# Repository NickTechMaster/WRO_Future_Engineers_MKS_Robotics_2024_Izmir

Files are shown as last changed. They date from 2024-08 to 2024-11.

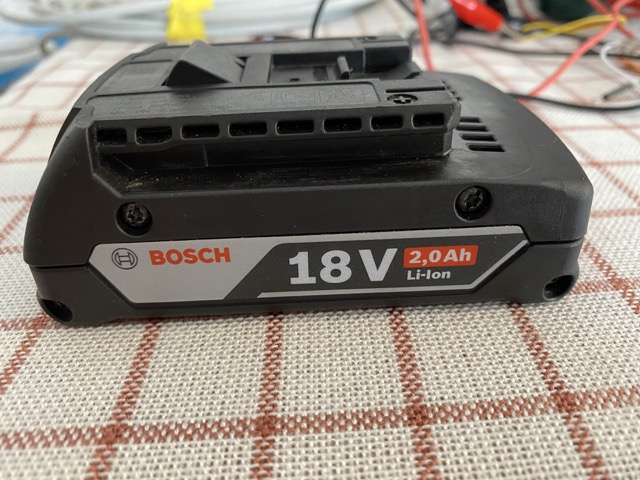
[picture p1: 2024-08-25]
2. Energy & Sensors/battery_1.jpeg

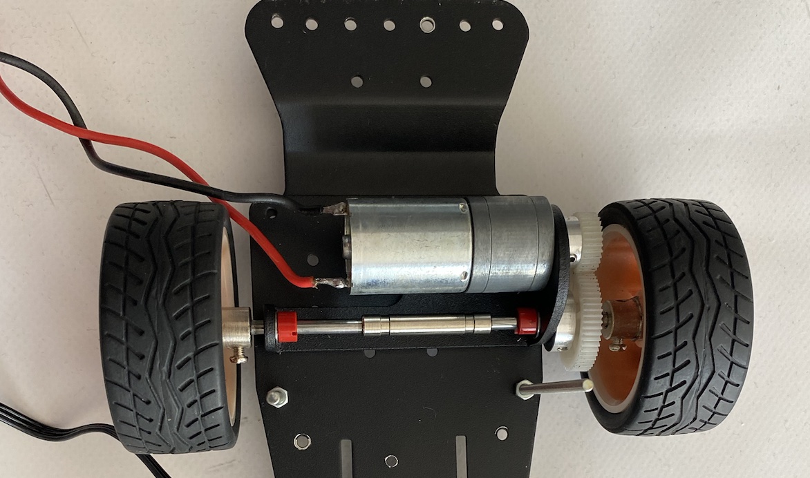
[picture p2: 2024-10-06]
1. Motorization/engine_1.jpg

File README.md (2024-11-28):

banner_Mks_Robotics-DownScaled

<h3>Infos of the GitHub Structure</h3>

Our GitHub documentation is structured according to the evaluation criteria of the WRO Future Engineers category. Under points 1-5, you will find information and materials that correspond to the evaluation criteria. Below that, under points a-f, we provide additional important information from our perspective.<br><hr>

<h3>Table of contents</h3>

[1. Motorization](https://github.com/NickTechMaster/WRO_Future_Engineers_MKS_Robotics_2024_Izmir/tree/main/1.%20Motorization
)<br>

[2. Energy & Sensors](https://github.com/NickTechMaster/WRO_Future_Engineers_MKS_Robotics_2024_Izmir/tree/main/2.%20Energy%20%26%20Sensors
)<br> 

[3. Obstacle Race](https://github.com/NickTechMaster/WRO_Future_Engineers_MKS_Robotics_2024_Izmir/tree/main/3.%20Obstacle%20Race%20
)<br>

[4. Photos](https://github.com/NickTechMaster/WRO_Future_Engineers_MKS_Robotics_2024_Izmir/tree/main/4.%20Photos
)<br>

[5. Videos](https://github.com/NickTechMaster/WRO_Future_Engineers_MKS_Robotics_2024_Izmir/tree/main/5.%20Videos
)<br>

[a. 3d printing](https://github.com/NickTechMaster/WRO_Future_Engineers_MKS_Robotics_2024_Izmir/tree/main/a.%203d%20printing
)<br>

[b. diagrams](https://github.com/NickTechMaster/WRO_Future_Engineers_MKS_Robotics_2024_Izmir/tree/main/b.%20diagrams
)<br>

[d. Code](https://github.com/NickTechMaster/WRO_Future_Engineers_MKS_Robotics_2024_Izmir/tree/main/d.%20Code
)<br>

[e. construction manual](https://github.com/NickTechMaster/WRO_Future_Engineers_MKS_Robotics_2024_Izmir/tree/main/e.%20construction%20manual
)<br>

[f. other](https://github.com/NickTechMaster/WRO_Future_Engineers_MKS_Robotics_2024_Izmir/tree/main/f.%20other
)<br>
<hr>

<h3>Introduction</h3>

We are Nico and Julian from Saarland, Germany, and this year we’re proud to once again compete as a team from Maximilian-Kolbe-Schule Wiebelskirchen, a secondary school, in the WRO (World Robot Olympiad) Future Engineers category. Robotics and engineering have been a big part of our lives for several years now, and our interest in this field has grown through numerous school-based projects and competitions.
Our WRO journey began back in 2019 when we participated in the "Mission" category. Though we didn’t qualify for the Germany Finals in our first two attempts, these experiences motivated us to improve and eventually try a new challenge: the "Future Engineers" category. Since making that switch, we’ve reached the national finals multiple times, and this year we reached a major milestone by winning second place at the Germany Finals, which qualified us for the World Finals.

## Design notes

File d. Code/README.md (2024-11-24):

**In this folder, you will find the programming for the robotic car.**

We are using two different Raspberry Pis, so we have a total of four scripts: two for the opening race and two for the obstacle race.

- **drive = driving Raspberry Pi**
- **cam = camera Raspberry Pi**

### Programming for the Opening Race

In this year's opening race, we are using the basic idea from last year. While driving, the robot continuously measures the values from the ultrasonic sensors located at the front, left, and right. Based on the values from the left and right sensors, the robot calculates the center point and steers the autonomous car proportionally to return it to the middle as efficiently as possible. This means that the further the car is from the center, the stronger it steers to get back to it.

For example: If the left ultrasonic sensor reads 10 and the right ultrasonic sensor reads 50, the left sensor is showing a very short distance, meaning the car is quite far to the left near the barrier. If we take the sum of both values, we get 60. Half of that is 30. When both sensors read 30, we know that the robot is exactly in the center. To reach this center, we calculate the percentage difference and steer accordingly.

Since this process is repeated very quickly and frequently, the car may sometimes sway slightly, but this is corrected by the system. To ensure the car stops perfectly after 3 laps, it increases a variable each time it takes a turn. We detect a turn when the color sensor detects orange or blue. The upper Raspberry Pi, which receives this data, sends it to the driving Raspberry Pi. The driving Raspberry Pi counts 12 turns and then continues until the front ultrasonic sensor detects a certain distance, at which point the car stops.

### Programming for the Obstacle Race

For the obstacle race, we use the programming from the opening race as the foundation, since we also need to drive autonomously here. Only when the camera detects a colored block does the upper Raspberry Pi send a signal to the driving Raspberry Pi, which then performs a corresponding evasive maneuver. We go around red blocks to the right and around green blocks to the left. Additionally, we detect turns using the color sensor, where we perform a realignment maneuver.

For color detection of the blocks, we use filters/masks to only see the relevant colors and filter out other potential errors the camera might detect. We then detect the contours of the objects. To adjust the color values of the masks, we wrote an additional script with sliders.

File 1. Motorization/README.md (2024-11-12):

**Motorization**

We used a Funduino kit as the foundation, specifically designed for Future Engineers. However, from this kit, we only used the base plates, distance sleeves, and the steering mechanism. The exact dimensions and measurements of the plates, screws, and other components can be found in the assembly instructions (e. Assembly Instructions).

**Steering**  
For steering, we use a 20-kg servo steering motor. This motor is mounted horizontally on our base plate. A small rod, secured with screws, runs from the servo’s thread to the actual steering axle. This axle connects the two front wheels. When the servo turns in one direction, the entire steering axle shifts, which in turn moves the wheels.

**Drive Motor**  
As the drive motor, we use a standard DC motor, which is operated via the motor controller "L298N." It is directly connected to the 18V battery. The motor is then powered by the motor driver. Three wires extend from the motor controller, which we use to control the motor, and they are connected directly to the controlling Raspberry Pi. The Pi sends a PWM signal. A PWM signal (Pulse Width Modulation) is an electrical signal that varies the "On" and "Off" duration to control power. To drive both wheels simultaneously, we use a gear transmission that transfers the motor’s rotations to a gear firmly attached to the drive axle. The drive axle is split in the middle, but the two ends are connected with a coupling sleeve. This allows one wheel to rotate freely. Previously, we encountered a problem where the car’s wheels would lock due to power issues. Now, with one wheel able to rotate freely, this issue occurs less frequently.

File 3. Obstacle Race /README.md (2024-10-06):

**Obstacle Race Programming**

In the obstacle race, we use a similar programming approach to the one from the opening race for the driving fundamentals, as we also aim to keep the car centered in the middle of the track as much as possible. To achieve this, the Raspberry Pi calculates an average position where the car would be in the middle. It then determines how far the car is from this center in terms of percentage. This percentage is then converted and passed on to the servo motor. Only when the camera detects a colored block, the Raspberry Pi connected to the camera sends a signal to the driving Raspberry Pi. The driving Raspberry Pi then executes a corresponding evasive maneuver. The signals are transmitted using on/off electrical signals. For example, the Raspberry Pi connected to the camera applies a 3-volt current to one of the wires between the two Raspberry Pis. The Raspberry Pis have built-in GPIO pins that send a HIGH signal to communicate. The driving Raspberry Pi checks if there is a current on one of the wires. Depending on which wire is affected, it performs different actions. For red blocks, it steers to the right, and for green blocks, it steers to the left. To detect the color of the blocks, we use filters/masks to isolate specific colors and filter out errors that the camera might detect. We then identify the contours. To set the color values of the masks, we wrote a separate program with sliders. Additionally, the car has several safety maneuvers that are triggered if the front ultrasonic sensors detect that the car is about to hit one of the blocks or the barrier. In such cases, the car reverses.

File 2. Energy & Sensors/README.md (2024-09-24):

**Energy**  
Our car is powered by a standard 18V Bosch battery. This battery is inserted into a battery holder, from which a connection leads to the voltage converter. The converter steps the voltage down to 5V, which we need for the Raspberry Pis, the servo motor, and the ultrasonic sensors. Additionally, a motor controller is used, which is powered directly by 18V. It's important to note that the ultrasonic sensors run on 5V, while other sensors, like the color sensor, operate on 3.3V. The color sensor communicates with the Raspberry Pis via an I²C signal. I²C (Inter-Integrated Circuit) is a serial communication bus that connects devices using two lines.

**Sensors**  
A variety of sensors are installed in our car. First, we have integrated three HCSR-04 ultrasonic sensors, which are used to detect the road and calculate steering. The Raspberry Pi sends GPIO signals to the ultrasonic sensors, waits for the return of the ultrasonic signal, and measures the time between the outgoing and incoming signals to calculate the distance. GPIO (General Purpose Input/Output) signals are digital input and output signals that can be generated or read by a microcontroller, like the Raspberry Pi, to control or communicate with external electronic components. Additionally, we have installed a color sensor that detects orange lines to count laps, allowing us to stop successfully after three laps. At the top, there is also a camera, a USB webcam from Logitech (Brio 500), which is used for obstacle detection. We selected this camera because of its wide-angle lens, exposure adjustment, and color rendering.

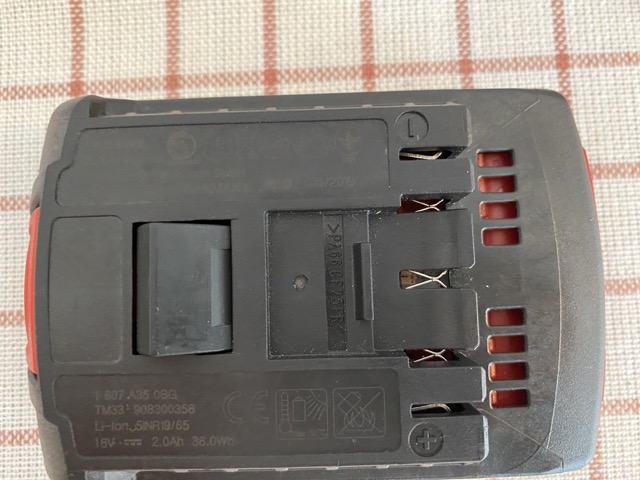
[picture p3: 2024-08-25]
2. Energy & Sensors/battery_2.jpeg

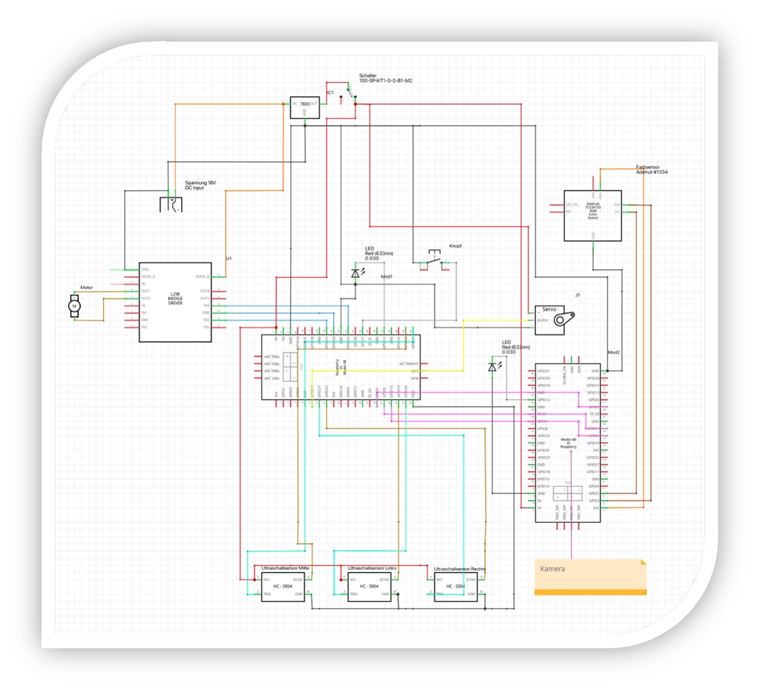
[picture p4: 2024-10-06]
2. Energy & Sensors/circuit_diagram_2.jpg

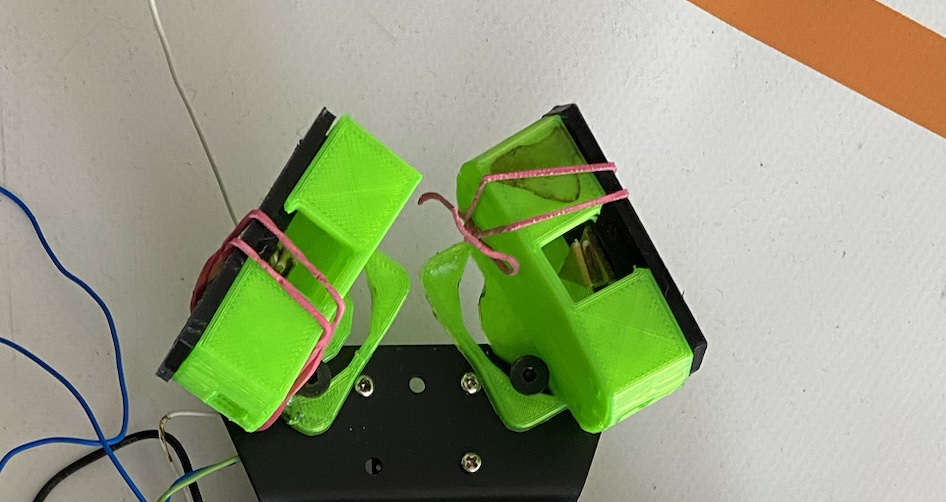
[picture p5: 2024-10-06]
2. Energy & Sensors/ultrasonic_sensor_holder_1.jpg

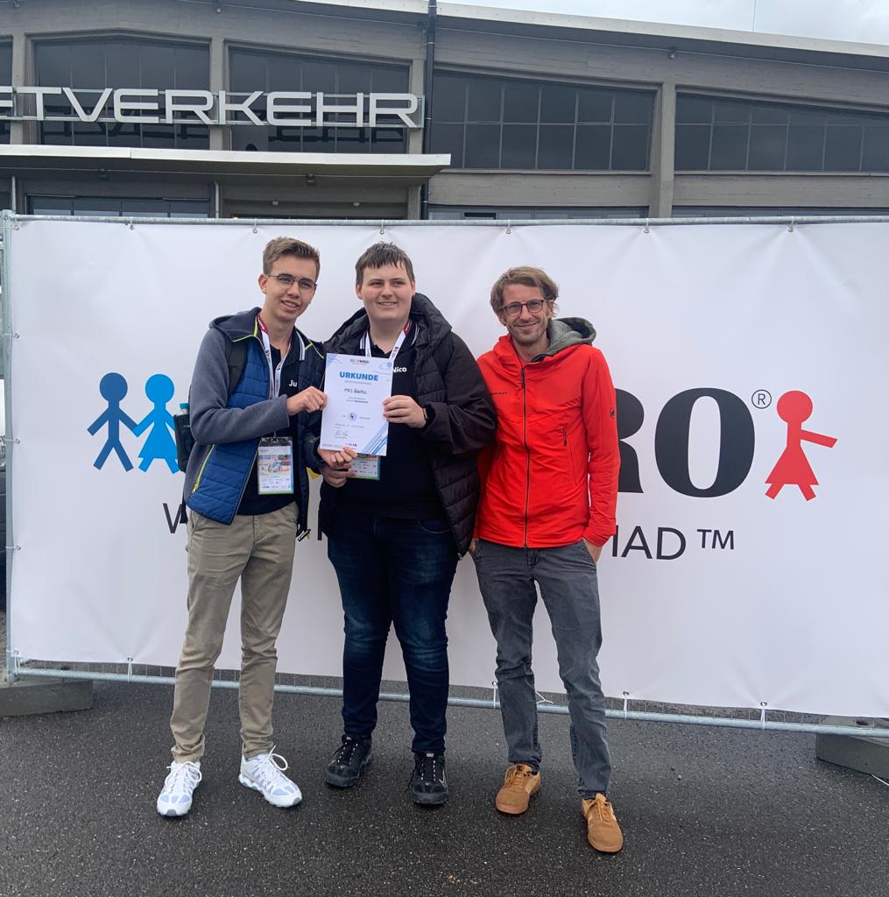
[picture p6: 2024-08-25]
f. other/Teamfoto.jpg

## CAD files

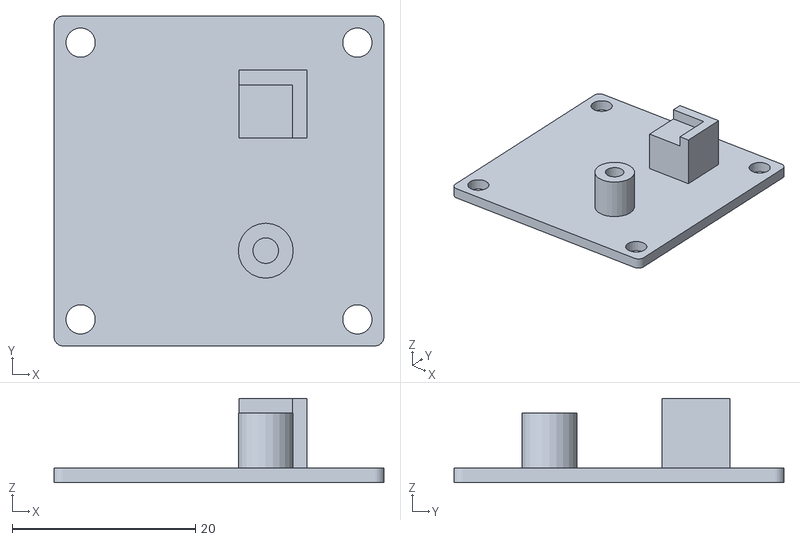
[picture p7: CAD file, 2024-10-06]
a. 3d printing/gyro sensor mount.stl
36.0 x 36.0 x 9.20

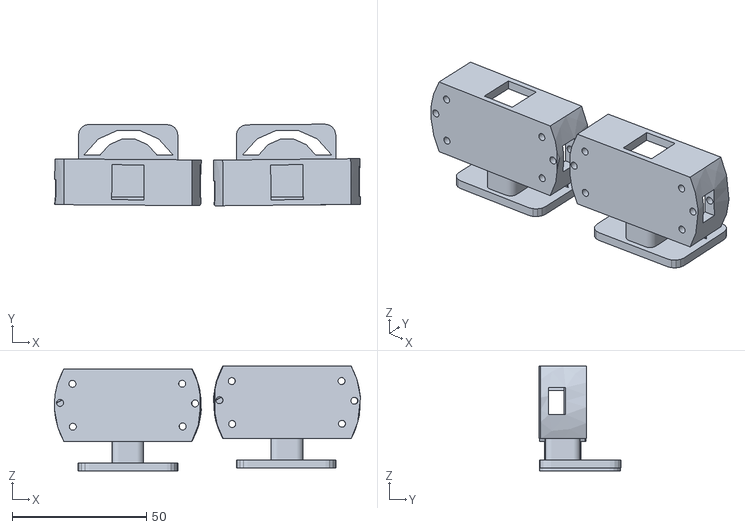
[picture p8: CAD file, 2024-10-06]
a. 3d printing/ultraschall.stl
113.8 x 30.4 x 39.0

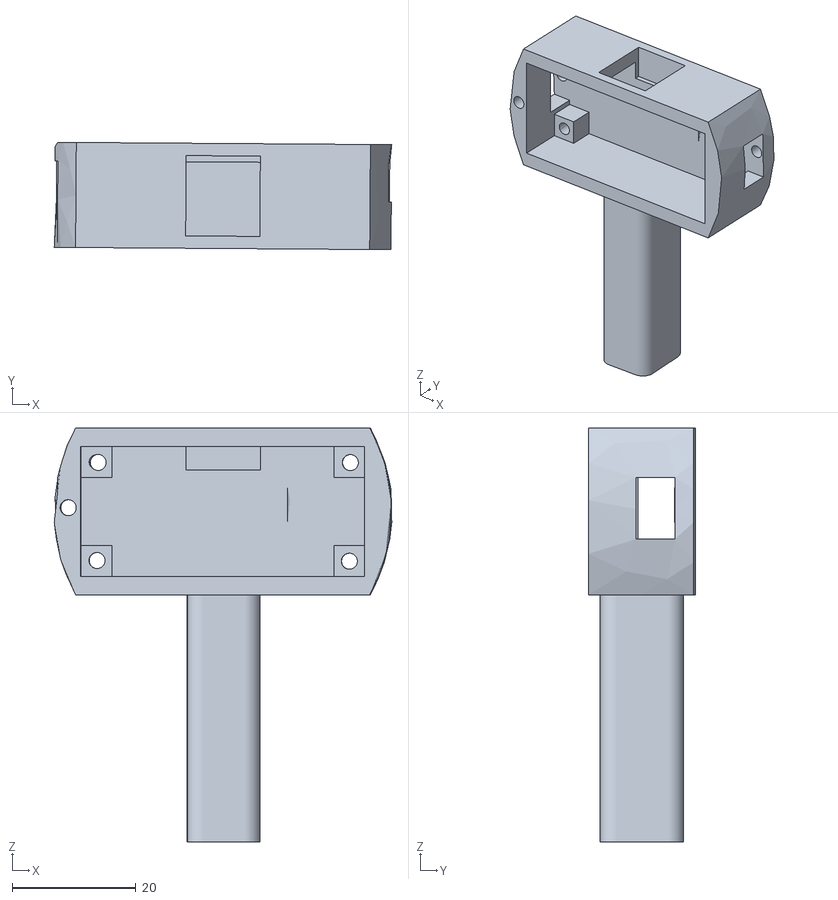
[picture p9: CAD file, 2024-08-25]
a. 3d printing/ultrasonic sensor bracket.stl
54.6 x 17.4 x 67.0

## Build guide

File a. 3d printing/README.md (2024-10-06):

Here you can find various 3D printing files of parts that we use for our robot car.

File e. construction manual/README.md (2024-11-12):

###  Hardware & Components 

| Quantity | Component | Price per Unit | Total Price |
|---|---|---|---|
| 2 | [Raspberry Pi 4](https://www.amazon.com/-/de/dp/B0899VXM8F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) | $86 | $172 |
| 1 | [Arduino Nano](https://www.amazon.com/-/de/dp/B0DFGR288F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) | $8 | $8 |
| 1 | [Gyro Sensor](https://www.amazon.com/-/de/dp/B07MMZ37PT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) | $5 | $5 |
| 1 | [Color Sensor](https://www.amazon.com/-/de/dp/B087Z3K6P5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) | $4 | $4 |
| 3 | [HC-SR04 Ultrasonic Sensor](https://www.amazon.com/-/de/dp/B0BDFLPZ2R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) | $4 | $12 |
| 1 | [Brushless Motor 12V](https://www.amazon.com/-/de/dp/B07D297L9F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) | $14 | $14 |
| 1 | [Servo Motor (A81BHP)](https://www.vgr-technology.de/p/agf-rc-servo-a81bhp-hochgeschwindigkeitslenkung-rc-servomotor-0-052-sec-23kg-programmierbar) | $95 | $95 |
| 1 | [Servo Motor small](https://www.amazon.com/-/de/dp/B0BKPL2Y21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) | $3 | $3 |
| 1 | [Motor Controller (L298N)](https://www.amazon.com/-/de/dp/B0CR6BX5QL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) | $4 | $4 |
| 1 | [18V Bosch Drill Battery](https://www.bosch-professional.com/de/de/products/gba-18v-2-0ah-1600Z00036) | $65 | $65 |
| 1 | [Voltage Converter (18V to 5V)](https://www.joy-it.net/de/products/SBC-Buck03](https://www.reichelt.de/de/de/entwicklerboards-spannungsregler-dc-dc-wandler-debo-dcdc-down-7-p333858.html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)) | $20 | $20 |
| 1 | [Button](https://www.amazon.com/-/de/dp/B08SQHRRDH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) | $2 | $2 |
| 1 | [Switch](https://www.amazon.com/-/de/dp/B00004WLKC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) | $8 | $8 |
| 2 | [LED Lamps](https://www.amazon.com/-/de/dp/B0BXKM8PN3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) | $1 | $2 |
| Various  | [Jumper Wires / Other Cables](https://www.amazon.com/-/de/dp/B01EV70C78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) | $5 | $5 |
| 1 | [USB Webcam (Logitech Brio 500)](https://www.amazon.com/-/de/dp/B0CPBD3PDD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) | $84 | $84 |

---

###  Other Components:

| Component | Price |
|---|---|
| [Metal Baseplate / Chassi](https://funduinoshop.com/diy-werkstatt/bausaetze/chassis/yfrobot-chassis-kit-mit-lenkachse)  | $50 |
| [Metal Standoffs](https://www.amazon.com/-/de/dp/B06Y5TJXY1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)  | $15 |
| [Self-modeled 3D Prints from a 3D Printer](https://www.amazon.com/-/de/dp/B0D421Q2Q2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) | $13 |
| [Various Screws](https://www.amazon.com/-/de/dp/B0BMQFHDBH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) | $10 |
| [Cable Ties](https://www.amazon.com/-/de/dp/B08TVLYB3Q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) | $5 |
| [Hot Glue / Super Glue / Metal Glue](https://www.amazon.com/-/de/dp/B09XY1WDTX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) | $10 |
| [Heat Shrink Tubing](https://www.amazon.com/-/de/dp/B0BG6V4HV4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) | $5 |

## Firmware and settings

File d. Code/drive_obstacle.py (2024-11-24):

# Import necessary libraries
import RPi.GPIO as GPIO   
import time
from gpiozero import Button, LED
import board
import busio
import adafruit_vl53l0x
from mpu6050 import mpu6050

# Initializing constants and variables
servo_cam_mitte = 70  # Initial servo position for camera
sensor = mpu6050(0x68)  # Initialize MPU6050 sensor for accelerometer
mittelpunkt = 0  # Variable to store midpoint value
GPIO.setwarnings(False)  # Disable GPIO warnings
GPIO.setmode(GPIO.BCM)  # Set GPIO pin numbering to BCM

# Setup motor control pins
in1, in2, en = 24, 23, 25
GPIO.setup(in1, GPIO.OUT)
GPIO.setup(in2, GPIO.OUT)
GPIO.setup(en, GPIO.OUT)
GPIO.output(in1, GPIO.LOW)
GPIO.output(in2, GPIO.LOW)
p = GPIO.PWM(en, 1000)  # PWM control for motor speed
p.start(0)  # Start PWM with 0% duty cycle (motor off)

# Setup servo control pins
servoPIN = 17
GPIO.setup(servoPIN, GPIO.OUT)
p_s = GPIO.PWM(servoPIN, 333)  # PWM for steering servo

servoPIN_cam = 18
GPIO.setup(servoPIN_cam, GPIO.OUT)
p_s_c = GPIO.PWM(servoPIN_cam, 333)  # PWM for camera servo

# Setup other GPIO pins for ultrasonic sensors and button inputs
GPIO.setup(21, GPIO.OUT)
GPIO.setup(20, GPIO.IN)
GPIO.setup(26, GPIO.OUT)
GPIO.setup(19, GPIO.IN)
GPIO.setup(27, GPIO.OUT)
GPIO.setup(22, GPIO.IN)
GPIO.setup(6, GPIO.IN)
GPIO.setup(4, GPIO.IN)
GPIO.setup(13, GPIO.OUT)
GPIO.output(13, GPIO.LOW)  # Initialize output pin 13 to LOW
GPIO.setup(9, GPIO.IN)
GPIO.setup(5, GPIO.IN)

# Ultrasonic function to calculate distance
def ultraschall(mode):
    global distanz
    countdown = 50000

    # Select pins based on mode (0, 1, 2)
    if mode == 0:
        GPIO_TRIGGER, GPIO_ECHO = 21, 20
    elif mode == 1:
        GPIO_TRIGGER, GPIO_ECHO = 26, 19
    else:
        GPIO_TRIGGER, GPIO_ECHO = 27, 22

    # Trigger ultrasonic sensor
    GPIO.output(GPIO_TRIGGER, True)
    time.sleep(0.00001)
    GPIO.output(GPIO_TRIGGER, False)

    StartZeit = time.time()
    StopZeit = time.time()

    # Wait for echo response and measure duration
    while GPIO.input(GPIO_ECHO) == 0:
        StartZeit = time.time()
        countdown -= 1
        if countdown <= 0:
            print(f"Ultrasonic error in mode {mode}")
            return 1200

    countdown = 7000
    while GPIO.input(GPIO_ECHO) == 1:
        StopZeit = time.time()
        countdown -= 1
        if countdown <= 0:
            print(f"Ultrasonic error in mode {mode}")
            return 1200

    # Calculate distance
    TimeElapsed = StopZeit - StartZeit
    distanz = (TimeElapsed * 34300) / 2
    return round(distanz)

# Initialize LEDs
led = LED(12)
led.on()

# Initialize button
button = Button(8)

# Wait for button press to start
while True:
    if button.is_pressed:
        p_s.start(60)
        p_s_c.start(servo_cam_mitte)
        print("Button pressed, starting motors and servos.")
        break
    else:
        pass

# Initialize control variables
countdown_2 = 25
forward = 0
red_stone, green_stone, purple_stone = 0, 0, 0
delay_vorne = 1
counter_sides, counter_after_curve = 10, 0
right, left = False, False
no_acceleration, no_acceleration_long, no_acceleration_counter_long = 0, 0, 0
countdown_cam = 0

# Main loop
while True:
    # Camera servo control based on countdown
    if countdown_cam < 3:
        p_s_c.ChangeDutyCycle(servo_cam_mitte)
    elif countdown_cam < 4:
        p_s_c.ChangeDutyCycle(servo_cam_mitte + 17)
    elif countdown_cam < 5:
        p_s_c.ChangeDutyCycle(servo_cam_mitte)
    elif countdown_cam < 6:
        p_s_c.ChangeDutyCycle(servo_cam_mitte - 17)
    else:
        countdown_cam = 0
    countdown_cam += 1

    # Read accelerometer data and detect movement
    accelerometer_data1 = sensor.get_accel_data()["x"] * (-1)
    time.sleep(0.1)
    accelerometer_data2 = sensor.get_accel_data()["x"] * (-1)
    accelerometer_data = abs(accelerometer_data1 - accelerometer_data2) / 0.1

    # If no significant acceleration, trigger motion detection
    if accelerometer_data < 3:
        no_acceleration += 1
    else:
        no_acceleration = 0

    # Handle case of long-term lack of acceleration
    if no_acceleration >= 10:
        print("No movement detected for a while.")
        p.ChangeDutyCycle(30)
        GPIO.output(in1, GPIO.LOW)
        GPIO.output(in2, GPIO.HIGH)
        p_s.ChangeDutyCycle(60)
        time.sleep(2)
        print("Warning: danger detected, moving back.")
        GPIO.output(in1, GPIO.HIGH)
        GPIO.output(in2, GPIO.LOW)
        no_acceleration_long += 1

    if no_acceleration_long >= 2:
        print("No movement detected for a long time.")
        p.ChangeDutyCycle(30)
        GPIO.output(in1, GPIO.LOW)
        GPIO.output(in2, GPIO.HIGH)
        p_s.ChangeDutyCycle(60)
        time.sleep(2)
        print("Warning: danger detected, moving back.")
        GPIO.output(in1, GPIO.HIGH)
        GPIO.output(in2, GPIO.LOW)
        no_acceleration_long = 0

    # Handle ultrasonic sensor readings and object detection
    vorne = ultraschall(3)
    if vorne > 1000:
        print("Error: ultrasonic sensor 3 returned too high value.")
        vorne = 50

    value_90 = ultraschall(1)
    if value_90 < 1000:
        if value_90 < 5.5:
            p.ChangeDutyCycle(30)
            GPIO.output(in1, GPIO.LOW)
            GPIO.output(in2, GPIO.HIGH)
            p_s.ChangeDutyCycle(60)
            time.sleep(1)
            print("Warning: danger detected in front (90 degrees).")
            GPIO.output(in1, GPIO.HIGH)
            GPIO.output(in2, GPIO.LOW)
        data_90 = value_90
    else:
        print("Error: ultrasonic sensor 1 returned too high value.")

    # Repeat for another ultrasonic sensor (270 degrees)
    value_270 = ultraschall(0)
    if value_270 < 1000:
        data_270 = value_270
        if value_270 < 5.5:
            p.ChangeDutyCycle(30)
            GPIO.output(in1, GPIO.LOW)
            GPIO.output(in2, GPIO.HIGH)
            p_s.ChangeDutyCycle(60)
            time.sleep(1)
            print("Warning: danger detected in front (270 degrees).")
            GPIO.output(in1, GPIO.HIGH)
            GPIO.output(in2, GPIO.LOW)
    else:
        print("Error: ultrasonic sensor 0 returned too high value.")

    # Handle steering logic based on ultrasonic data
    if data_270 != 0 and data_90 != 0 and data_270 < 5500 and data_90 < 5500:
        mittelpunkt = (data_270 + data_90) / 2  # Calculate the midpoint between sensors

        # Adjust the steering based on sensor readings
        if mittelpunkt < 100:
            GPIO.output(13, GPIO.HIGH)
        else:
            GPIO.output(13, GPIO.LOW)

        # If the robot is near an obstacle, adjust direction accordingly
        if mittelpunkt > 280 and counter_sides <= 0 and vorne < 50:
            p.ChangeDutyCycle(30)
            p_s.ChangeDutyCycle(60)
            x = 0
            while x < 12:
                time.sleep(0.1)
                vorne = ultraschall(3)
                if vorne > 1000:
                    print("Error: value too high for front sensor")
                    vorne = 50
                if vorne < 20:  # If the front is blocked, take action to avoid it
                    if delay_vorne == 1:
                        delay_vorne = 0
                    else:
                        p.ChangeDutyCycle(30)
                        GPIO.output(in1, GPIO.LOW)
                        GPIO.output(in2, GPIO.HIGH)
                        p_s.ChangeDutyCycle(60)
                        time.sleep(0.5)
                        print("Danger ahead!")
                        GPIO.output(in1, GPIO.HIGH)
                        GPIO.output(in2, GPIO.LOW)
                x += 1
            # Adjust steering based on sensor readings
            if data_90 > data_270:
                p_s.ChangeDutyCycle(69)
                right = True
            else:
                p_s.ChangeDutyCycle(53)
                left = True
            GPIO.output(in1, GPIO.LOW)
            GPIO.output(in2, GPIO.HIGH)
            time.sleep(2)
            p_s.ChangeDutyCycle(60)
            time.sleep(0.2)
            GPIO.output(in1, GPIO.HIGH)
            GPIO.output(in2, GPIO.LOW)
            counter_sides = 22
            counter_after_curve = 10
        else:
            counter_sides -= 1  # Decrease the side counter if no obstacle is detected

    # Adjust steering based on distance readings
    if data_270 <= data_90:
        lenkung = round(100 - (100 * data_270 / mittelpunkt))
        if lenkung > 5:
            einlenkung = round(60 - lenkung * var_lenkung_r)
            if einlenkung >= 20:
                p_s.ChangeDutyCycle(einlenkung - 3)
            else:
                p_s.ChangeDutyCycle(53)
        else:
            p_s.ChangeDutyCycle(60)

    elif data_90 <= data_270:
        lenkung = round(100 - (100 * data_90 / mittelpunkt))
        if lenkung > 5:
            einlenkung = round(60 + lenkung * var_lenkung_l)
            if einlenkung <= 50:
                p_s.ChangeDutyCycle(einlenkung + 3)
            else:
                p_s.ChangeDutyCycle(69)
        else:
            p_s.ChangeDutyCycle(60)

    # Handle red stone detection
    if GPIO.input(6) == GPIO.HIGH:
        red_stone += 1
    else:
        red_stone = 0

    # Handle green stone detection
    if GPIO.input(4) == GPIO.HIGH:
        green_stone += 1
    else:
        green_stone = 0

    # Handle purple stone detection
    if GPIO.input(5) == GPIO.HIGH:
        purple_stone += 1
    else:
        purple_stone = 0

    # Handle purple stone color handling
    if purple_stone > 1:  # Check if there are more than 1 purple stones detected
        red_stone = 0  # Reset red stone count
        green_stone = 0  # Reset green stone count
        vanished_purple = 0  # Initialize counter for vanished purple stones
    
        while vanished_purple < 6:  # Keep looking for purple stones until 6 vanish
            vorne = ultraschall(3)  # Get distance from front ultrasonic sensor (sensor 3)
            print(str(vanished_purple) + " purple")  # Print the current count of vanished purple stones
    
            if GPIO.input(5) == GPIO.LOW:  # If the sensor detects a change (stone lost)
                vanished_purple += 1  # Increment the vanished counter
    
            if vorne < 35:  # If an obstacle is too close (less than 35 cm)
                p.ChangeDutyCycle(30)  # Slow down the motor
                GPIO.output(in1, GPIO.LOW)
                GPIO.output(in2, GPIO.HIGH)  # Reverse the robot
                p_s.ChangeDutyCycle(60)  # Adjust the servo speed
    
                time.sleep(1)  # Wait for 1 second
                print("gefahr_purple")  # Danger message for purple stone
                GPIO.output(in1, GPIO.HIGH)
                GPIO.output(in2, GPIO.LOW)  # Move forward again
                p.ChangeDutyCycle(tempo_stein)  # Set motor speed back to normal
    
            # Left side sensor (1)
            value = ultraschall(1)
            if value < 1000:  # If a valid sensor reading is obtained
                if value < 8:  # If obstacle is too close (less than 8 cm)
                    p.ChangeDutyCycle(30)
                    GPIO.output(in1, GPIO.LOW)
                    GPIO.output(in2, GPIO.HIGH)  # Reverse
                    p_s.ChangeDutyCycle(60)
                    time.sleep(1)  # Wait
                    print("gefahr_ultraschall")  # Danger message for left sensor
                    GPIO.output(in1, GPIO.HIGH)
                    GPIO.output(in2, GPIO.LOW)  # Move forward again
                data_90 = value  # Store the distance data
    
            time.sleep(0.05)  # Short delay
    
            # Right side sensor (0)
            value = ultraschall(0)
            if value < 1000:  # If a valid sensor reading is obtained
                data_270 = value  # Store the distance data
                if value < 8:  # If obstacle is too close
                    p.ChangeDutyCycle(30)
                    GPIO.output(in1, GPIO.LOW)
                    GPIO.output(in2, GPIO.HIGH)  # Reverse
                    p_s.ChangeDutyCycle(60)
                    time.sleep(1)  # Wait
                    print("gefahr_ultraschall")  # Danger message for right sensor
                    GPIO.output(in1, GPIO.HIGH)
                    GPIO.output(in2, GPIO.LOW)  # Move forward again
    
            # Steering adjustment for turning based on sensor data
            if data_270 <= data_90:
                lenkung = round(100 - (100 * data_270 / mittelpunkt))  # Calculate steering angle
                if lenkung > 5:
                    einlenkung = round(60 - lenkung * var_lenkung_r)  # Adjust steering for right turns
                    if einlenkung >= 20:
                        p_s.ChangeDutyCycle(einlenkung - 3)  # Apply steering adjustment
                    else:
                        p_s.ChangeDutyCycle(53)  # Neutral steering
                else:
                    p_s.ChangeDutyCycle(60)  # Straight steering
    
            # Steering adjustment for left turns
            elif data_90 <= data_270:
                lenkung = round(100 - (100 * data_90 / mittelpunkt))  # Calculate steering angle
                if lenkung > 5:
                    einlenkung = round(60 + lenkung * var_lenkung_l)  # Adjust steering for left turns
                    if einlenkung <= 50:
                        p_s.ChangeDutyCycle(einlenkung + 3)  # Apply steering adjustment
                    else:
                        p_s.ChangeDutyCycle(70)  # Stronger turn
                else:
                    p_s.ChangeDutyCycle(60)  # Neutral steering

    # Handle red stone color handling
    if red_stone >= 1:  # Check if a red stone is detected
        counter_red = 0  # Initialize counter for red stone detection
        vanished = 0  # Initialize counter for missing red stones
        print("____________________________")
        print("red")  # Print message for red stone detection
        time.sleep(0.05)
    
        p.ChangeDutyCycle(tempo_stein)  # Set motor speed for red stone handling
    
        while ultraschall(1) > 14:  # Continue if the front distance is greater than 14 cm
            if GPIO.input(9) == GPIO.HIGH:  # If the stop button is pressed, break the loop
                print("break color")
                break
            time.sleep(0.05)
            vorne = ultraschall(3)  # Get distance from front sensor
            time.sleep(0.05)
    
            if GPIO.input(6) != GPIO.HIGH:  # If sensor 6 is not active, increment vanished count
                vanished += 1
    
            p_s.ChangeDutyCycle(50)  # Adjust servo speed
            counter_red += 1  # Increment red stone counter
    
            if vorne < 35:  # If an obstacle is too close (less than 35 cm)
                p.ChangeDutyCycle(30)
                GPIO.output(in1, GPIO.LOW)
                GPIO.output(in2, GPIO.HIGH)  # Reverse
                p_s.ChangeDutyCycle(60)
                time.sleep(1)  # Wait
                print("gefahr_red")  # Danger message for red stone
                GPIO.output(in1, GPIO.HIGH)
                GPIO.output(in2, GPIO.LOW)  # Move forward again
                p.ChangeDutyCycle(tempo_stein)
    
            print(f"counter red: {counter_red}    vanished: {vanished}")  # Debug output
    
            if counter_red > 35:  # If red stone counter exceeds threshold, adjust servo
                print(counter_red)
                p_s.ChangeDutyCycle(68)  # Adjust servo speed
                time.sleep(0.5)  # Wait
                counter_red = 0  # Reset red stone counter
    
            if vanished > 3:  # If more than 3 vanished red stones, stop the loop
                print("abgebrochen")  # Break message
                p_s.ChangeDutyCycle(68)  # Adjust servo speed
                time.sleep(0.5)  # Wait
                vanished = 0  # Reset vanished counter
                break  # Exit loop
    
        print("ende")  # End of red stone processing
        print("____________________________")
        
    else:
        counter_red = 0 # Reset counter
        p.ChangeDutyCycle(tempo) # Change motor speed

    # Handle green stone color handling   
    if green_stone >= 1:  # Check if a green stone is detected
        counter_red = 0  # Reset red stone counter
        vanished = 0  # Reset vanished counter
        print("____________________________")
        print("green")  # Print message for green stone detection
        time.sleep(0.05)
    
        p.ChangeDutyCycle(tempo_stein)  # Set motor speed for green stone handling
    
        while ultraschall(0) > 18:  # Continue if the right distance is greater than 18 cm
            if GPIO.input(9) == GPIO.HIGH:  # If stop button is pressed, break the loop
                print("break color")
                break
            time.sleep(0.05)
            vorne = ultraschall(3)  # Get distance from front sensor
            time.sleep(0.05)
    
            if GPIO.input(4) != GPIO.HIGH:  # If sensor 4 is not active, increment vanished count
                vanished += 1
    
            p_s.ChangeDutyCycle(69)  # Adjust servo speed for green stone
            counter_red += 1  # Increment green stone counter
    
            if vorne < 30:  # If obstacle is too close (less than 30 cm)
                p.ChangeDutyCycle(30)
                GPIO.output(in1, GPIO.LOW)
                GPIO.output(in2, GPIO.HIGH)  # Reverse
                p_s.ChangeDutyCycle(60)
                time.sleep(1)  # Wait
                print("gefahr_green")  # Danger message for green stone
                GPIO.output(in1, GPIO.HIGH)
                GPIO.output(in2, GPIO.LOW)  # Move forward again
    
            print(f"counter green: {counter_red}    vanished: {vanished}")  # Debug output
    
            if counter_red > 15:  # If green stone counter exceeds threshold, adjust servo
                print(counter_red)
                p_s.ChangeDutyCycle(55)  # Adjust servo speed
                time.sleep(0.5)  # Wait
                counter_red = 0  # Reset green stone counter
    
            if vanished > 3:  # If more than 3 vanished green stones, stop the loop
                print("abgebrochen")  # Break message
                p_s.ChangeDutyCycle(55)  # Adjust servo speed
                time.sleep(0.5)  # Wait
                vanished = 0  # Reset vanished counter
                break  # Exit loop
    
        print("ende")  # End of green stone processing
        print("____________________________")
    
        p_s.ChangeDutyCycle(57)  # Reset servo speed
        
    else:
        counter_red = 0 # Reset counter
        p.ChangeDutyCycle(tempo) # Change motor speed

    var_delay = 0.05  # Short delay between actions
    
    if vorne < 13:  # If an obstacle is detected too close in front
        if delay_vorne == 1:  # If there is a delay, reverse the flag
            delay_vorne = 0
        else:
            p.ChangeDutyCycle(30)  # Slow down
            GPIO.output(in1, GPIO.LOW)
            GPIO.output(in2, GPIO.HIGH)  # Reverse
            p_s.ChangeDutyCycle(60)
            time.sleep(1.3)  # Wait
            print("gefahr")  # Danger message
            GPIO.output(in1, GPIO.HIGH)
            GPIO.output(in2, GPIO.LOW)  # Move forward again
    
    p.ChangeDutyCycle(tempo)  # Set motor speed back to normal
    
    time.sleep(var_delay)  # Short delay before the next iteration

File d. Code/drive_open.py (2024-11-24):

# Import necessary libraries
import RPi.GPIO as GPIO   
import time
from gpiozero import Button, LED
from mpu6050 import mpu6050

# Initialize the MPU6050 sensor
sensor = mpu6050(0x68)

# Setup initial state variables
mittelpunkt = 0

# Disable GPIO warnings
GPIO.setwarnings(False)

# Set GPIO pin numbering to BCM
GPIO.setmode(GPIO.BCM)

# Motor control pins
in1 = 24
in2 = 23
en = 25
temp1 = 1

# Setup motor control pins as output
GPIO.setup(in1, GPIO.OUT)
GPIO.setup(in2, GPIO.OUT)
GPIO.setup(en, GPIO.OUT)

# Initialize motor pins to stop the motor
GPIO.output(in1, GPIO.LOW)
GPIO.output(in2, GPIO.LOW)

# Setup PWM for motor speed control
p = GPIO.PWM(en, 1000)
p.start(0)

# Setup servo control pin
servoPIN = 17
GPIO.setup(servoPIN, GPIO.OUT)
p_s = GPIO.PWM(servoPIN, 333)

# Setup additional GPIO pins for ultrasonic sensors and button
GPIO.setup(7, GPIO.OUT)
GPIO.setup(14, GPIO.OUT)
GPIO.setup(15, GPIO.IN)

GPIO.setup(21, GPIO.OUT)
GPIO.setup(20, GPIO.IN)

GPIO.setup(26, GPIO.OUT)
GPIO.setup(19, GPIO.IN)

GPIO.setup(9, GPIO.IN)

# Setup additional ultrasonic sensor pins
GPIO.setup(27, GPIO.OUT)
GPIO.setup(22, GPIO.IN)

# Function to trigger ultrasonic sensor and measure distance
def ultraschall(mode):
    global distanz
    countdown = 500000

    # Set ultrasonic sensor trigger and echo pins based on mode
    if mode == 0:
        GPIO_TRIGGER = 21
        GPIO_ECHO = 20
    elif mode == 1:
        GPIO_TRIGGER = 26
        GPIO_ECHO = 19
    else:
        GPIO_TRIGGER = 27
        GPIO_ECHO = 22

    GPIO.output(GPIO_TRIGGER, True)
    time.sleep(0.00001)
    GPIO.output(GPIO_TRIGGER, False)

    # Measure time between trigger and echo signal
    StartZeit = time.time()
    StopZeit = time.time()

    countdown = 300000

    # Wait for the echo signal to start
    while GPIO.input(GPIO_ECHO) == 0:
        StartZeit = time.time()
        countdown -= 1
        if countdown <= 0:
            print("Error in sensor")
            return 1200

    # Wait for the echo signal to stop
    while GPIO.input(GPIO_ECHO) == 1:
        StopZeit = time.time()
        countdown -= 1
        if countdown <= 0:
            print("Error in sensor")
            return 1200

    # Calculate distance based on time difference
    TimeElapsed = StopZeit - StartZeit
    distanz = (TimeElapsed * 34300) / 2

    return round(distanz)

# Setup initial motor direction
GPIO.output(in1, GPIO.HIGH)
GPIO.output(in2, GPIO.LOW)

# Initialize sensor data
data_90 = 0
data_270 = 0

# Initialize button and LED
button = Button(8)
led = LED(12)
led.on()

# Wait for the button to be pressed to start the servo
while True:
    if button.is_pressed:
        p_s.start(60)
        print("Start")
        break
    else:
        pass
        
# Set initial servo duty cycle
p_s.ChangeDutyCycle(60)

# Initialize counters for curve and no-movement detection
curves = 0
countdown = 2
countdown_2 = 1
delay_vorne = 1

no_acceleration = 0
no_acceleration_long = 0
no_acceleration_counter_long = 0

# Main loop for handling movement logic
while True:
    # Read accelerometer data
    accelerometer_data = sensor.get_accel_data()
    accelerometer_data1 = accelerometer_data["x"] * (-1)
    time.sleep(0.1)
    accelerometer_data = sensor.get_accel_data()
    accelerometer_data2 = accelerometer_data["x"] * (-1)

    # Calculate acceleration difference
    accelerometer_data = abs(accelerometer_data1 - accelerometer_data2) / 0.1

    if accelerometer_data < 3:
        no_acceleration += 1
    else:
        no_acceleration = 0

    if accelerometer_data >= 3:
        no_acceleration_long = 0

    # Detect prolonged inactivity
    if no_acceleration >= 10:
        print("No movement detected")
        p_s.ChangeDutyCycle(60)
        time.sleep(2)
        no_acceleration = 0
        no_acceleration_long += 1

    # If no movement for a long time, change motor behavior
    if no_acceleration_long >= 2:
        print("No movement for long")
        p.ChangeDutyCycle(27)
        GPIO.output(in1, GPIO.LOW)
        GPIO.output(in2, GPIO.HIGH)
        p_s.ChangeDutyCycle(60)
        time.sleep(2)
        print("Danger detected")
        GPIO.output(in1, GPIO.HIGH)
        GPIO.output(in2, GPIO.LOW)
        no_acceleration_long = 0
        no_acceleration_counter_long = 0

    # Track the number of curves and stop when finished
    if curves >= 12:
        countdown_2 -= 1
        print(f"End in {countdown_2} seconds")

    countdown -= 1
    if GPIO.input(9) == GPIO.HIGH and countdown <= 0:
        curves += 1
        print(f"Curve {curves}")
        countdown = 25
        if curves == 12:
            countdown_2 = 15
    if curves == 12 and countdown_2 <= 0:
        p.ChangeDutyCycle(0)
        p_s.stop()

    # Set steering control variables
    var_delay = 0
    var_lenkung_r = 0.15
    var_lenkung_l = 0.15
    g = 10

    # Measure distance for 90 and 270 degree angles
    value = ultraschall(1)
    if value < 1000:
        data_90 = value
        print(f"Data 90: {data_90}")
    else:
        print("Error: value too high")

    value = ultraschall(0)
    if value < 1000:
        data_270 = value
        print(f"Data 270: {data_270}")
    else:
        print("Error: value too high")

    # Adjust steering based on distance data
    if data_270 != 0 and data_90 != 0 and data_270 < 5500 and data_90 < 5500:
        calc = round((((((100 - ((100 * data_90) / (((data_270 + data_90) / 2)))) / 10)) ** 7) / g)

        # Limit steering adjustment
        if calc > 5:
            if calc > 100 or calc < -100:
                calc = 100
            p_s.ChangeDutyCycle(60 + abs(calc) * var_lenkung_r)
            time.sleep(0.001)
        elif calc < -15:
            if calc > 100 or calc < -100:
                calc = -100
            p_s.ChangeDutyCycle(60 - abs(calc) * var_lenkung_l)
            time.sleep(0.001)
        else:
            p_s.ChangeDutyCycle(60)

    # Update motor speed
    p.ChangeDutyCycle(35)

    # Small delay 
    time.sleep(var_delay)
